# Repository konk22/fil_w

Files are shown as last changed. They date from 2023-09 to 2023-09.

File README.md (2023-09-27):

# fil_w
Кронштейн для пластика с датчиком веса, дисплеем, энкодером и подключением к HA на базе ESPHome. 

Снимок экрана 2023-09-27 214616

Устройство умеет:

  1. Замеряет вес катушки филамента;
  2. Выводит текущий вес на дисплей;
  3. Вносит корректировку веса пустой катушки;
  4. Дублирует данные в HA;
  5. Позволяет проводить калибровку как с помощью энкодера, так и с помощью HA и настраивать вес калибровочной груза;
  6. Позволяет проводить корректировку и точную настройку калибровки как с помощью энкодера так и с помощью HA;
  7. Получает профили филамента из HA для автоматической корректировки веса пустой катушки;
  8. Каждые 12 сек выводит прогресс выполненного задания печати на экран на 2 сек.

В проекте используются:

  1.  Датчик веса HX711 не менее 10кг (лучше 20кг);
  2.  OLED дисплей 128X64 I2C SSD1306 (расстояние между крепежным отверстиями 23мм);
  3.  Энкодер, на круглой плате;
  4.  Wemos d1 mini ESP32;
  5.  Подшипник F623ZZ - 12шт;
  6.  Резьбовая втулка под винт 3мм - 3шт;
  7.  Винт м3*16 - 6шт;
  8.  Винт м3*6 - 3шт;
  9.  Винт м4*20 - 2шт;
  10. Винт м5*20 - 2шт.









1. Для работы с профилями филамента необходимо добавить вспомогательный объект (список - input_select) в HA. Пример: "FDplast 2500/350" После символа "/" идет вес пустой катушки, до символа "/" может идти любой текст, но не слишком длинный, так как он не поместится по длинне на экран.
2. Для корректной работы необходимо зайти в Настройки -> Устройства и службы -> ESPHome, нажать кнопку "Настройки" напротив устройства Fil_w и отметить чекбокс "Разрешите устройству обращаться к службам Home Assistant."

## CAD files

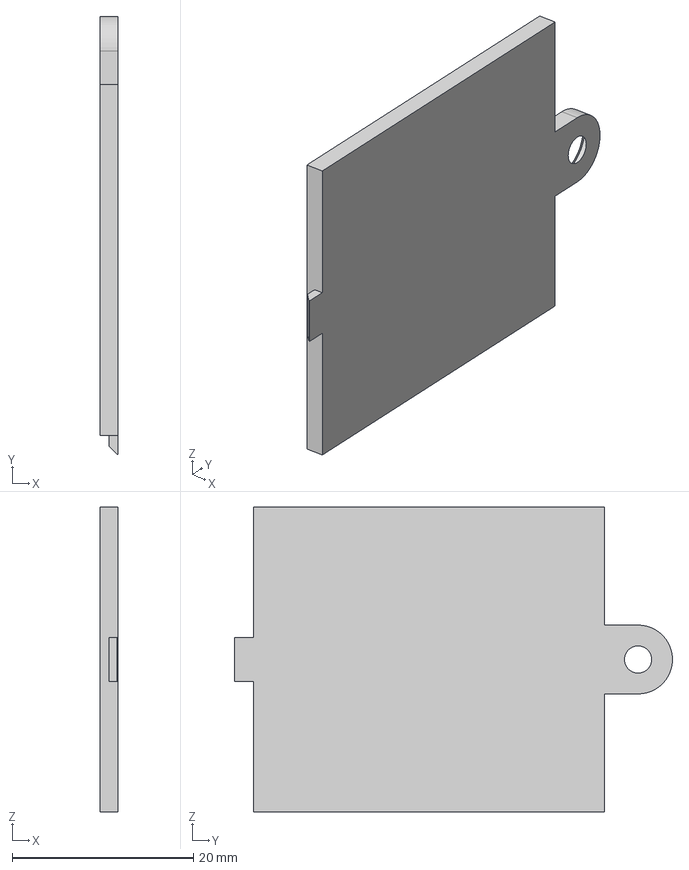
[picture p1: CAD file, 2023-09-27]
step/Крышка.step
2.00 x 48.3 x 33.6 mm

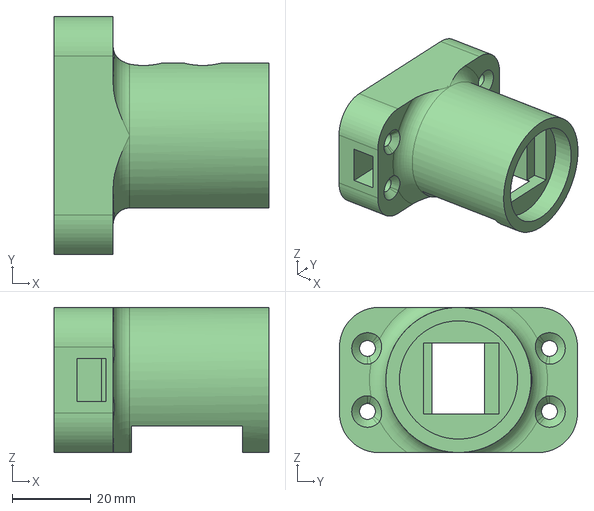
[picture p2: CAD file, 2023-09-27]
step/Основание правое.step
54.5 x 60.4 x 36.8 mm

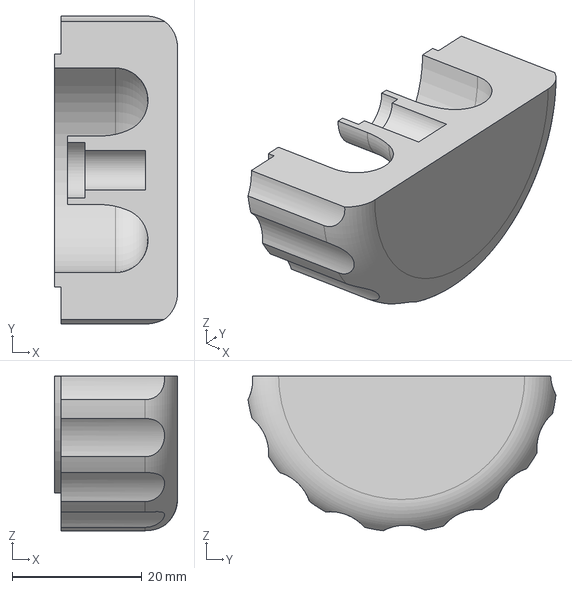
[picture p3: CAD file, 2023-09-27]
step/Ручка энкодера.step
19.0 x 47.6 x 23.9 mm

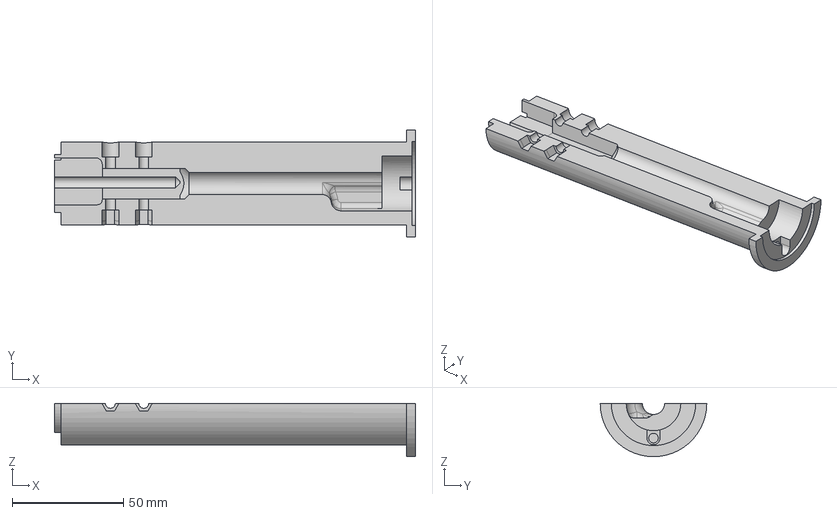
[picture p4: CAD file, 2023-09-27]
step/Рычаг длинный.step
162.5 x 48.0 x 24.0 mm

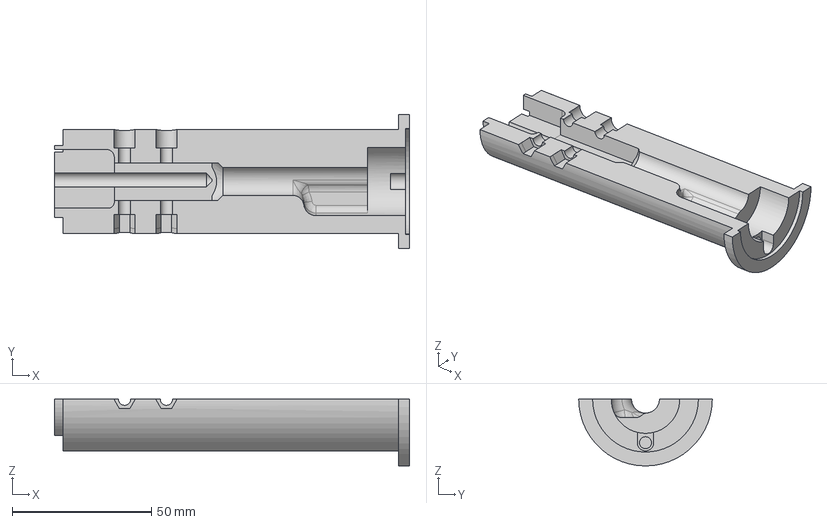
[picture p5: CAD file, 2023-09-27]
step/Рычаг короткий.step
127.5 x 48.0 x 24.0 mm

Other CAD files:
step/Крепеж энкодера.step
step/основание.step

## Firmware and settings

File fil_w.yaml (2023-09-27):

esphome:
  name: fil-w-v2
  friendly_name: fil_w_v2

esp32:
  board: esp32dev
  framework:
    type: arduino

# Enable logging
logger:
  level: WARN
# Enable Home Assistant API
api:
  encryption:
    key: "  "

ota:
  password: "  "

wifi:
  ssid: !secret wifi_ssid
  password: !secret wifi_password

  # Enable fallback hotspot (captive portal) in case wifi connection fails
  ap:
    ssid: "Fil-W-V2 Fallback Hotspot"
    password: "Password"

captive_portal:

i2c:
  sda: 21
  scl: 22
  frequency: 800000

font:
  - file: "fonts/arialmt.ttf"
    id: font53
    size: 53
    glyphs: |-
      !"%()+=,-_.>?:°0123456789АБВГДЕЁЖЗИЙКЛМНОПРСТУФХЦЧЩЬЫЪЭЮЯABCDEFGHIJKLMNOPQRSTUVWXYZ абвгдеёжзийклмнопрстуфхцчшщьыъэюяabcdefghijklmnopqrstuvwxyz'éèàòùç/&ôœìïöñ
  - file: "fonts/arialmt.ttf"
    id: font18
    size: 18
    glyphs: |-
      !"%()+=,-_.>?:°0123456789АБВГДЕЁЖЗИЙКЛМНОПРСТУФХЦЧЩЬЫЪЭЮЯABCDEFGHIJKLMNOPQRSTUVWXYZ абвгдеёжзийклмнопрстуфхцчшщьыъэюяabcdefghijklmnopqrstuvwxyz'éèàòùç/&ôœìïöñ
  - file: "fonts/arialmt.ttf"
    id: font14
    size: 14
    glyphs: |-
      !"%()+=,-_.>?:°0123456789АБВГДЕЁЖЗИЙКЛМНОПРСТУФХЦЧЩЬЫЪЭЮЯABCDEFGHIJKLMNOPQRSTUVWXYZ абвгдеёжзийклмнопрстуфхцчшщьыъэюяabcdefghijklmnopqrstuvwxyz'éèàòùç/&ôœìïöñ
  - file: "fonts/arialmt.ttf"
    id: font16
    size: 16
    glyphs: |-
      !"%()+=,-_.>?:°0123456789АБВГДЕЁЖЗИЙКЛМНОПРСТУФХЦЧЩЬЫЪЭЮЯABCDEFGHIJKLMNOPQRSTUVWXYZ абвгдеёжзийклмнопрстуфхцчшщьыъэюяabcdefghijklmnopqrstuvwxyz'éèàòùç/&ôœìïöñ

globals:
  - id: processed_flag
    type: bool
    restore_value: no
    initial_value: "false"

  - id: filament_list_split2
    type: float
    restore_value: no
    initial_value: "0"

  - id: ref_tare_zero
    type: float
    restore_value: no
    initial_value: "0"

  - id: ref_tare_1kg
    type: float
    restore_value: no
    initial_value: "0"

  - id: last_weight_val
    type: float
    restore_value: no
    initial_value: "0"

  - id: profile_bool
    type: bool
    restore_value: no
    initial_value: "false"

  - id: prog_print
    type: bool
    restore_value: no
    initial_value: "false"

interval:
  - interval: 12s
    then:
      if: 
        condition:
          lambda: return id(state_print).state == "printing";
        then:
          - lambda: id(prog_print) = true;
          - delay: 2s
          - lambda: id(prog_print) = false;
        else:
          - lambda: id(prog_print) = false;
  - interval: 5min
    then:
      if: 
        condition:
          display.is_displaying_page: main_page
        then:
          display.page.show: !lambda return id(main_page);

sensor:
  - platform: hx711
    name: "internal hx711"
    dout_pin: 33
    clk_pin: 23
    gain: 128
    update_interval: 0.2s 
    internal: true  
    filters:
      - filter_out: 8388607
      - median:
          window_size: 3
          send_every: 2
          send_first_at: 2
      - exponential_moving_average:
          alpha: 0.5
          send_every: 1
          send_first_at: 1
    id: fil_w_raw

  - platform: template
    name: "internal plastic"
    update_interval: 0.1s
    lambda: |-
      float x = (id(fil_w_raw).state - id(tare_zero).state) / (id(tare_1kg).state - id(tare_zero).state) * id(ref_tare_kg).state;
      return x;
    filters:
      - exponential_moving_average:
          alpha: 0.9
          send_every: 2
          send_first_at: 1
      - delta: 1.5 
    internal: true   
    id: fil_w_f

  - platform: template
    name: "internal raw calibrate"
    update_interval: 0.1s
    lambda: return id(fil_w_raw_calib).state = id(fil_w_raw).state;
    internal: true   
    id: fil_w_raw_calib

  - platform: template
    name: "Plastic"
    unit_of_measurement: г
    update_interval: 3s
    lambda: |-
      return id(filament_weight).state = id(fil_w_f).state - id(weight_coil).state;  
    id: filament_weight
    
  - platform: template
    name: "HX711"
    update_interval: 3s
    lambda: |-
      return id(hx711_weight).state = id(fil_w_raw).state;   
    id: hx711_weight

  - platform: homeassistant
    id: progress_print
    entity_id: sensor.uni3d_progress    # задать имя объекта прогресса печати из HA

  - platform: rotary_encoder
    pin_a:
      number: 19        # поменять местами с pin_b для инвертирования энкодера
      inverted: false
      mode:
        input: true
        #pullup: true
    pin_b:
      number: 18        # поменять местами с pin_a для инвертирования энкодера
      inverted: false
      mode:
        input: true
        #pullup: true
    resolution: 1       # разрешение энкодера 1, 2, 4
    restore_mode: ALWAYS_ZERO
    on_clockwise:
      then:
        - script.execute: script_on_clockwise
    on_anticlockwise:
      then:
        - script.execute: script_on_anticlockwise
    id: my_rotary_encoder
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
